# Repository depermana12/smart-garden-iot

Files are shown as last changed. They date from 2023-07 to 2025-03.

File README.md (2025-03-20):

Project ini dibuat sebagai tugas akhir dengan fokus smart garden

## Demo
[Demo alat](https://www.youtube.com/watch?v=bV-0lBpWv4o)

# Tujuan Penelitian
Bertujuan untuk merancang, membuat, mengimplementasi sistem otomasi penyiraman air dan pemupukan cair di dalam mini greenhouse berbasis IoT (Internet of Things).

## Deskripsi singkat

Jadwal penyemprotan pupuk cair menggunakan sensor RTC DS3231, kendali aktuator berdasarkan kelembapan tanah yang menggunakan sensor capacitive soil moisture v1.2, pemrosesan data sensor dilakukan mikrokontroler ESP32. Paket data dikirim menggunakan protocol MQTT ke node-Red Dashboard berbasis web.

Pemantauan dan kendali set point dilakukan pada web. node-RED di-hosting di server dengan nginx sebagai reverse proxy ke domain iot.depermana.com.

## Metode Penelitian
Menggunakan metode rekayasa teknik dengan pengambilan data secara observasi laboratorium. Dimulai dari perancangan, pembuatan, dan pengujian. 

Penerapan penyiraman air menggunakan pendekatan metode metode Blaney-Criddle sebagai perhitungan teoritis kebutuhan air tanaman dengan data iklim BMKG di daerah penelitian. Data tersebut dijadikan acuan kebutuhan penyiraman air

## Perancangan
### blok diagram


### skematik
Imgur

### pcb shield
Imgur

### miniatur green house
Imgur

# Fitur Utama
- Penyiraman otomatis berdasarkan data kelembaban tanah.
- Pemupukan otomatis dengan jadwal yang dapat disesuaikan.
- water level tangki air dan pupuk cair
- suhu dan kelembapan udara GH
- Monitoring kondisi tanaman secara real-time.
- Kendali jarak jauh melalui web.
- data logger menggunakan time series database influx-db

## Teknologi yang Digunakan
- Mikrokontroller ESP32.
- Protokol MQTT broker mosquitto.
- Sensor kelembaban tanah capacitive soil moisture v1.2.
- RTC DS3231
- Sensor ultrasonik HC-SR04
- Sensor suhu dan kelembapan udara DHT 33
- Platform IoT (server running ubuntu, nginx webserver, node-Red, tld, lets encrypt).

# Tantangan Utama
- satu sensor kelembapan tanah tidak dapat merepresentasi keseluruhan nilai kelembapan tanah. Solusi menggunakan lebih dari 1 sensor kelembapan tanah dibeberapa titik tanah dan nilai terseut dirata-rata
- Keamanan sistem IoT untuk melindungi data dan perangkat.

# Hasil Penelitian
Proyek ini berhasil menghasilkan sistem yang dapat memberikan penyiraman dan pemupukan otomatis untuk tanaman berdasarkan kondisi kelembapan tanah dan jadwal pemupukan cair yang dapat ditentukan pengguna. Sistem ini juga memberikan akses jauh melalui internet untuk pengawasan dan kendali.

Imgur

Imgur 

Imgur

Imgur

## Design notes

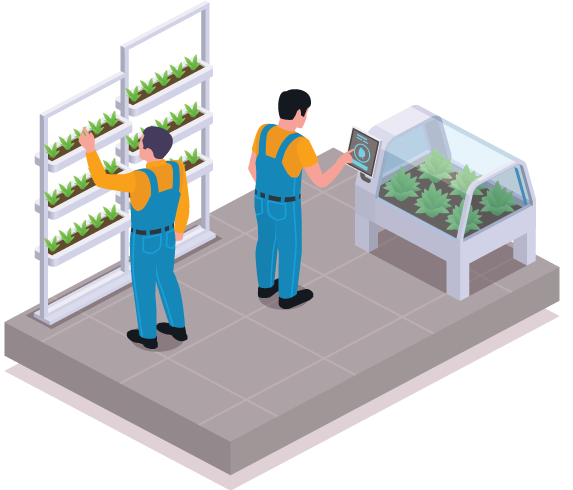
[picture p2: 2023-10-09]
frontend/landing_page/assets/images/right-image.png

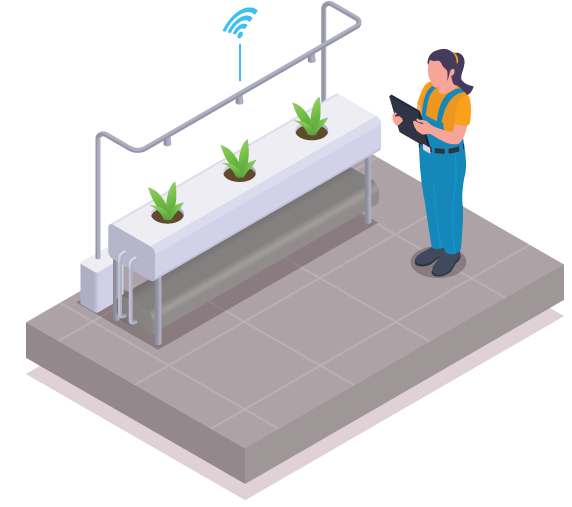
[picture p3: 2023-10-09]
frontend/landing_page/assets/images/left-image.png

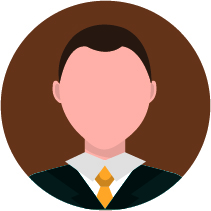
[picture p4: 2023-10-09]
frontend/landing_page/assets/images/member-02.jpg

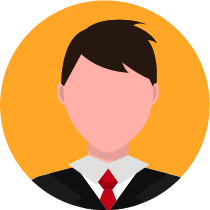
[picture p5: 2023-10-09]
frontend/landing_page/assets/images/member-01.jpg

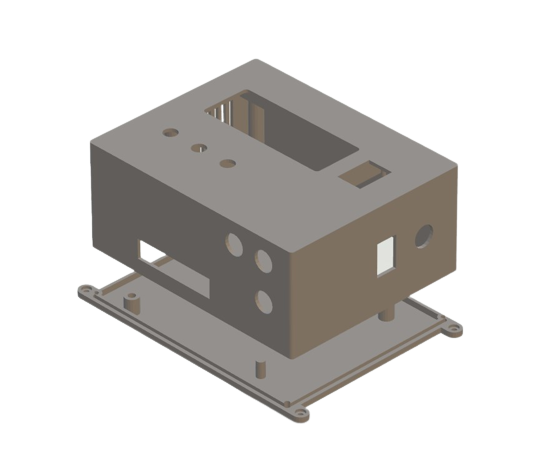
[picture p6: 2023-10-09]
case/casing device.png

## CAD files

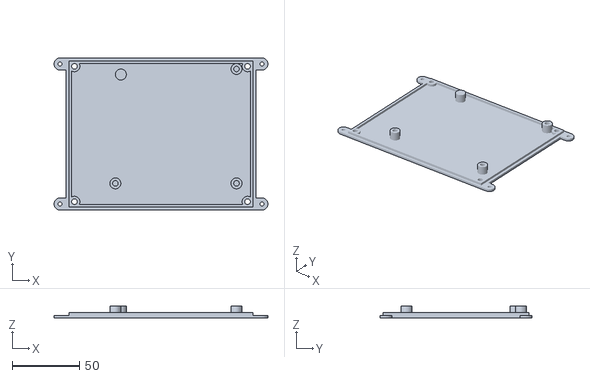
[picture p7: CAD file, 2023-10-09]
case/casing-device-3dp/casing-B.stl
159.0 x 113.0 x 9.00

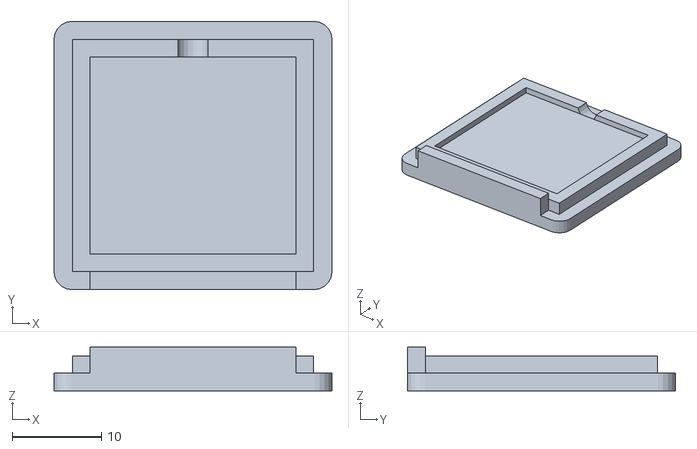
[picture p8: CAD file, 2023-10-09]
case/soil-moisture-3dp/SM-T.stl
31.1 x 30.0 x 4.90

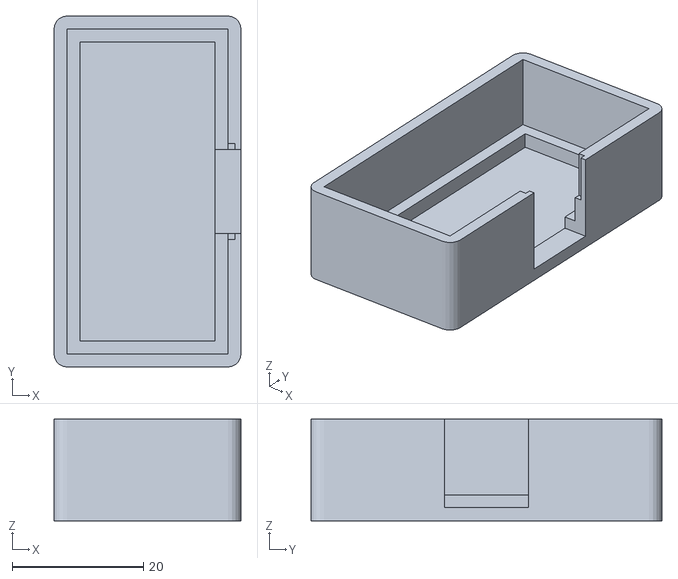
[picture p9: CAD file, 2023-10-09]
case/ultrasonic-case-3dp/USB.stl
28.5 x 53.5 x 15.5

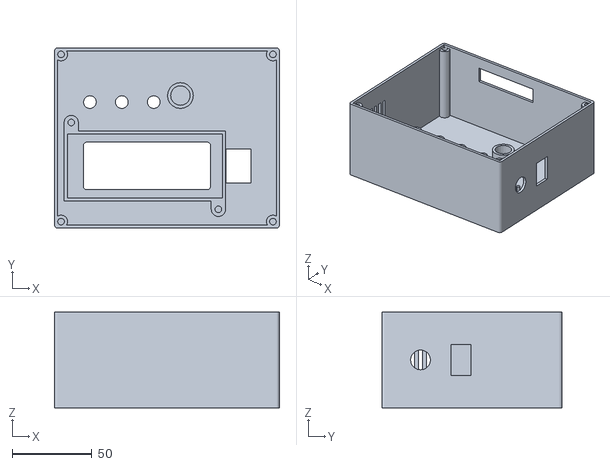
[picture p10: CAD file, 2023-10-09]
case/casing-device-3dp/casing-T.stl
141.0 x 113.0 x 60.0

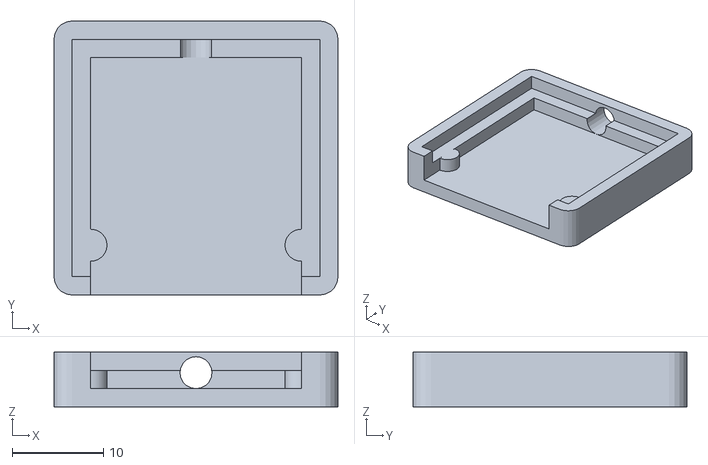
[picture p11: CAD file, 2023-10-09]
case/soil-moisture-3dp/SM-B.stl
31.1 x 30.0 x 6.00

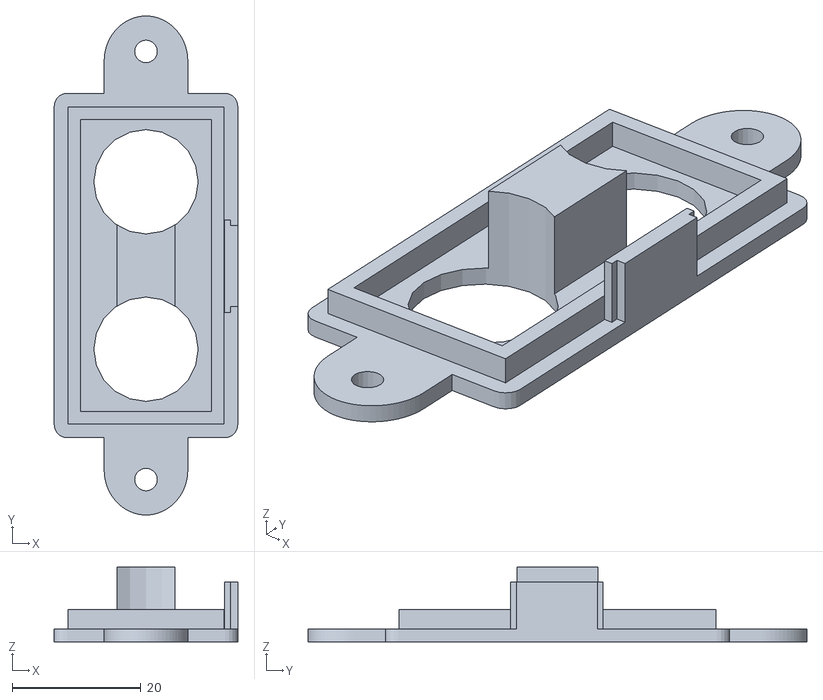
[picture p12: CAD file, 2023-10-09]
case/ultrasonic-case-3dp/UST.stl
28.5 x 77.5 x 11.6

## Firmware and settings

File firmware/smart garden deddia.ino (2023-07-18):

// Deddia Permana
// Changelog History
//
// 19.11.2022
// replaced broken ic ds3231SN RTC
// adjusting calibrating ds3231SN using syncroTime software
// removed poor charging circuit R 201 in RTC board
// 20.11.2022
// fixed relay D2 and D4 active low, setup to high after initialization
// 21.11.2022
// tweaking soil moisture v1.2 into 480khz
// replaced ne555 ic into tlc555 original TI
// 22.11.2022
// created custom charachter icon lcd
// DHT22 set to 2000 millis because hardware low sampling
// 23.11.2022
// Replacing Liquid crystal I2C library with hd44780 library
// added timing for lcd backlight on and off
// added depth and distance calculation of water tank and fertilizer tank
// constrain 1-100 percentage soil humidity
// 24.11.2022
// added multiple screen page in lcd
// 25.11.2022
// integrating nodered
// 8.12.2022
// switching to preferences library, EEPROM deprecated
// 13.12.2022
// added nodes persist to save latest set value
// touch up css dashboard
// 14.12.2022 - 27.12.2022
// refactor


/*
*
* dear future me
* when you write this code you were so motivated, add this and that, tinkering this and that.
* i know when we met again, you will be like wtf is this function, how is it work, where is the config directory and such.
* you have an ego to simplify a function and refuse to elaborate with a comments.
*
*
* Here i'am lol, fck
* glad that right now i have openai to explain my own code wkwkwk
*
*/

#include <SPI.h>
#include <Preferences.h>
#include <NewPing.h>
#include "DHT.h"
#include <Wire.h>
#include <hd44780.h>
#include <hd44780ioClass/hd44780_I2Cexp.h>
#include "RTClib.h"
#include <WiFi.h>
#include <AsyncTCP.h>
#include <ESPAsyncWebServer.h>
extern "C" {
#include "freertos/FreeRTOS.h"
#include "freertos/timers.h"
}
#include <AsyncMqttClient.h>

#define SONAR_NUM 2
#define DHTPIN 33
#define DHTTYPE DHT22
#define MQTT_HOST IPAddress(159, 223, 57, 199)
#define MQTT_USERNAME "depermana"
#define MQTT_PASSWORD "gundam123"
#define MQTT_PORT 1883

// Publish Topics
#define MQTT_PUB_TEMP "garden/dht22/temperature"
#define MQTT_PUB_HUM "garden/dht22/humidity"
#define MQTT_PUB_SOIL "garden/soil/soilHum"
#define MQTT_PUB_WATERK "garden/hcsr04/waterK"
#define MQTT_PUB_WATERJ "garden/hcsr04/waterJ"
#define MQTT_PUB_FERTK "garden/hcsr04/fertilizerK"
#define MQTT_PUB_FERTJ "garden/hcsr04/fertilizerJ"
#define MQTT_PUB_LOGW "garden/log/watering"

// Subscribe Topics
#define MQTT_SUB_REL1 "garden/relay/ch1"  // water
#define MQTT_SUB_REL3 "garden/relay/ch3"  // fertilizer
#define MQTT_SUB_TRES "garden/soil/setPoint"
#define MQTT_SUB_MONTH1 "garden/time/fertM1"
#define MQTT_SUB_MONTH2 "garden/time/fertM2"
#define MQTT_SUB_MONTH3 "garden/time/fertM3"
#define MQTT_SUB_DAY1 "garden/time/fertD1"
#define MQTT_SUB_DAY2 "garden/time/fertD2"
#define MQTT_SUB_DAY3 "garden/time/fertD3"
#define MQTT_SUB_HTIME "garden/time/fertH"
#define MQTT_SUB_MTIME "garden/time/fertMin"
#define MQTT_SUB_DURA "garden/time/duration"
#define MQTT_SUB_WTRT "garden/time/watering"

// BOILER PLATE WIFI MANAGER START //

#define _ESPASYNC_WIFIMGR_LOGLEVEL_ 3
#define DISPLAY_STORED_CREDENTIALS_IN_CP false
#include <esp_wifi.h>
#include <WiFiClient.h>
#include <WiFiMulti.h>
WiFiMulti wifiMulti;
#define USE_LITTLEFS true
#define USE_SPIFFS false

#if USE_LITTLEFS
#include "FS.h"
#include <LittleFS.h>

FS *filesystem = &LittleFS;
#define FileFS LittleFS
#define FS_Name "LittleFS"

#endif

//////

#define ESP_getChipId() (ESP.getChipId())
#define FORMAT_FILESYSTEM false
#define MIN_AP_PASSWORD_SIZE 8
#define SSID_MAX_LEN 32
#define PASS_MAX_LEN 64

typedef struct
{
  char wifi_ssid[SSID_MAX_LEN];
  char wifi_pw[PASS_MAX_LEN];
} WiFi_Credentials;

typedef struct
{
  String wifi_ssid;
  String wifi_pw;
} WiFi_Credentials_String;

#define NUM_WIFI_CREDENTIALS 5


typedef struct
{
  WiFi_Credentials WiFi_Creds[NUM_WIFI_CREDENTIALS];
  uint16_t checksum;
} WM_Config;

WM_Config WM_config;

#define CONFIG_FILENAME F("/wifi_cred.dat")
//////

bool initialConfig = false;
#define USE_AVAILABLE_PAGES false
#define USE_STATIC_IP_CONFIG_IN_CP false
#define USE_ESP_WIFIMANAGER_NTP false
#define USE_CLOUDFLARE_NTP false
#define USING_CORS_FEATURE false

////////////////////////////////////////////

// Use USE_DHCP_IP == true for dynamic DHCP IP, false to use static IP which you have to change accordingly to your network
#if (defined(USE_STATIC_IP_CONFIG_IN_CP) && !USE_STATIC_IP_CONFIG_IN_CP)
// Force DHCP to be true
#if defined(USE_DHCP_IP)
#undef USE_DHCP_IP
#endif
#define USE_DHCP_IP true
#else
// You can select DHCP or Static IP here
#define USE_DHCP_IP true
//#define USE_DHCP_IP     false
#endif

#if (USE_DHCP_IP)
// Use DHCP
#if (_ESPASYNC_WIFIMGR_LOGLEVEL_ > 3)
#warning Using DHCP IP
#endif

IPAddress stationIP = IPAddress(0, 0, 0, 0);
IPAddress gatewayIP = IPAddress(192, 168, 2, 1);
IPAddress netMask = IPAddress(255, 255, 255, 0);

#endif

////////////////////////////////////////////

#define USE_CONFIGURABLE_DNS false

IPAddress dns1IP = gatewayIP;
IPAddress dns2IP = IPAddress(8, 8, 8, 8);

#define USE_CUSTOM_AP_IP false

IPAddress APStaticIP = IPAddress(192, 168, 100, 1);
IPAddress APStaticGW = IPAddress(192, 168, 100, 1);
IPAddress APStaticSN = IPAddress(255, 255, 255, 0);

#include <ESPAsync_WiFiManager.h>

// SSID and PW for Config Portal
String ssid = "smart garden";
String password = "smartgarden123";

// SSID and PW for your Router
String Router_SSID;
String Router_Pass;

WiFi_AP_IPConfig WM_AP_IPconfig;
WiFi_STA_IPConfig WM_STA_IPconfig;

// BOILER PLATE WIFI MANAGER END //

unsigned long previousMillisBL = 0;
unsigned long intervalBL = 60000;
unsigned long previousMillis1 = 0;
unsigned long previousMillis2 = 0;
unsigned long interval1 = 10000;
unsigned long interval2 = 10000;
unsigned long intervalPolling = 1000;
unsigned long previousMillisFert = 0;
unsigned long previousMillisWtr = 0;
unsigned long previousMillisCheckFert = 0;
unsigned long previousPing0 = 0;
unsigned long previousPing1 = 0;

const int LCD_COLS = 20;
const int LCD_ROWS = 4;
const int waterPump = 16;
const int fertilizerPump = 2;
const int PingPin1 = 13;
const int EchoPin1 = 27;
const int PingPin2 = 25;
const int EchoPin2 = 26;
const int MAX_DISTANCE = 23;
const int waterTankDepth = 22;
const int waterTankLength = 19;
const int waterTankWidth = 19;
const int fertilizerTankDepth = 22;
const int fertilizerTankLength = 19;
const int ferilizerTankWidth = 19;
const int buttonLeft = 18;
const int buttonRight = 19;
const int soilMoisture = 32;
const int AirValue = 3506;
const int WaterValue = 1658;

int tanggal, bulan, tahun, jam, menit, detik, suhu, t, h;
int jadwalBulan1, jadwalBulan2, jadwalBulan3, jadwalTanggal1, jadwalTanggal2, jadwalTanggal3, setJam, setMenit;
int soilMoistRaw, soilMoistPercen, soilMoistSetpoint;
int gapSensor = 5;
int percenWaterDepth;
int intervalFertilizer;
int intervalWatering = 5000;
int lcdPageCounter = 1;

float waterMax, waterMin, waterGap;
float waterVolume, fertilizerVolume, waterDistance, fertilizerDistance, waterDepth, fertilizerDepth;

String hari, myDate, myTime, myTemp;

bool currentButtonLeft = LOW;
bool lastButtonLeft = LOW;
bool lastButtonRight = LOW;
bool currentButtonRight = LOW;
bool enableChange = true;
bool backlight = HIGH;
bool overrideCh1 = false;
bool overrideCh3 = false;
bool fertilizerPumpOn = false;
bool wateringOn = false;
bool soilMoistureTriggerActive = false;
bool debounce(bool last, int pin) {
  boolean current = digitalRead(pin);
  if (last != current) {
    delay(10);
    current = digitalRead(pin);
  }
  return current;
}

// Custom LCD Character
byte soilHum[] = { B00100, B01110, B11111, B11111, B10101, B00100, B11111, B11111 };
byte tempHum[] = { B00100, B01010, B01010, B01110, B01110, B11111, B11111, B01110 };
byte dateClock[] = { B00000, B01110, B10101, B10101, B10111, B10001, B01110, B00000 };
byte pupuk[] = { B01100, B01100, B01000, B00000, B10001, B11111, B11111, B11111 };
byte air[] = { B00100, B01110, B01010, B00000, B10001, B11111, B11111, B11111 };
byte kelembapan[] = { B00000, B00100, B01110, B11111, B11111, B11111, B01110, B00000 };

char daysOfTheWeek[7][12] = { "Minggu", "Senin", "Selasa", "Rabu", "Kamis", "Jumat", "Sabtu" };

NewPing sonar[SONAR_NUM] = {
  // Sensor object array.
  NewPing(PingPin1, EchoPin1, MAX_DISTANCE),
  NewPing(PingPin2, EchoPin2, MAX_DISTANCE)
};

// Instance
Preferences preferences;
DHT dht(DHTPIN, DHTTYPE);
hd44780_I2Cexp lcd;
RTC_DS3231 rtc;
AsyncMqttClient mqttClient;
TimerHandle_t mqttReconnectTimer;
TimerHandle_t wifiReconnectTimer;

void setup() {
  checkSensors();
  preferences.begin("smTres", false);
  Serial.begin(115200);
  dht.begin();
  pinMode(waterPump, OUTPUT);
  pinMode(fertilizerPump, OUTPUT);
  digitalWrite(waterPump, HIGH); // turn off relay when init
  digitalWrite(fertilizerPump, HIGH);
  // LCD custom character
  lcd.createChar(0, soilHum);
  lcd.createChar(1, tempHum);
  lcd.createChar(2, dateClock);
  lcd.createChar(3, pupuk);
  lcd.createChar(4, air);
  lcd.createChar(5, kelembapan);
  lcd.home();

  // MQTT calback function
  mqttReconnectTimer = xTimerCreate("mqttTimer", pdMS_TO_TICKS(2000), pdFALSE, (void *)0, reinterpret_cast<TimerCallbackFunction_t>(connectToMqtt));
  wifiReconnectTimer = xTimerCreate("wifiTimer", pdMS_TO_TICKS(2000), pdFALSE, (void *)0, reinterpret_cast<TimerCallbackFunction_t>(connectToWifi));
  WiFi.onEvent(WiFiEvent);
  mqttClient.onConnect(onMqttConnect);
  mqttClient.onDisconnect(onMqttDisconnect);
  mqttClient.onSubscribe(onMqttSubscribe);
  mqttClient.onMessage(onMqttMessage);
  mqttClient.onPublish(onMqttPublish);
  mqttClient.setServer(MQTT_HOST, MQTT_PORT);
  mqttClient.setCredentials(MQTT_USERNAME, MQTT_PASSWORD);
  connectToWifi();
  setupWifiManager();
}

void loop() {
  multiPageLCD();
  loopWifiManager();

  // Publish sensor data every 10 second
  unsigned long currentMillis1 = millis();
  if (currentMillis1 - previousMillis1 >= interval1) {
    checkTempRh();
    checkSoilMoisture();
    checkTank();

    // Publish an MQTT message on topic garden/dht22/temperature
    uint16_t packetIdPub1 = mqttClient.publish(MQTT_PUB_TEMP, 1, true, String(t).c_str());
    Serial.printf("Publishing on topic %s at QoS 1, packetId: %i", MQTT_PUB_TEMP, packetIdPub1);
    Serial.printf("Message: %.2f \n", t);
    // Publish an MQTT message on topic garden/dht22/humidity
    uint16_t packetIdPub2 = mqttClient.publish(MQTT_PUB_HUM, 1, true, String(h).c_str());
    Serial.printf("Publishing on topic %s at QoS 1, packetId %i: ", MQTT_PUB_HUM, packetIdPub2);
    Serial.printf("Message: %.2f \n", h);
    // Publish an MQTT message on topic garden/soil/temperature
    uint16_t packetIdPub3 = mqttClient.publish(MQTT_PUB_SOIL, 0, true, String(soilMoistPercen).c_str());
    Serial.printf("Publishing on topic %s at QoS 1, packetId: %i", MQTT_PUB_SOIL, packetIdPub3);
    Serial.printf("Message: %.2f \n", soilMoistPercen);

    previousMillis1 = currentMillis1;
  }

  // Publish sensor every 10 second
  unsigned long currentMillis2 = millis();
  if (currentMillis2 - previousMillis2 >= interval2) {
    // Publish an MQTT message on topic garden/hcsr04/water
    uint16_t packetIdPub4 = mqttClient.publish(MQTT_PUB_WATERK, 1, true, String(waterDepth).c_str());
    Serial.printf("Publishing on topic %s at QoS 1, packetId: %i", MQTT_PUB_WATERK, packetIdPub4);
    Serial.printf("Message: %.2f \n", waterDepth);
    // Publish an MQTT message on topic garden/hcsr04/water
    uint16_t packetIdPub5 = mqttClient.publish(MQTT_PUB_WATERJ, 1, true, String(waterDistance).c_str());
    Serial.printf("Publishing on topic %s at QoS 1, packetId: %i", MQTT_PUB_WATERJ, packetIdPub5);
    Serial.printf("Message: %.2f \n", waterDistance);
    // Publish an MQTT message on topic garden/hcsr04/fertilizer
    uint16_t packetIdPub6 = mqttClient.publish(MQTT_PUB_FERTK, 1, true, String(fertilizerDepth).c_str());
    Serial.printf("Publishing on topic %s at QoS 1, packetId: %i", MQTT_PUB_FERTK, packetIdPub6);
    Serial.printf("Message: %.2f \n", fertilizerDepth);
    // Publish an MQTT message on topic garden/hcsr04/fertilizer
    uint16_t packetIdPub7 = mqttClient.publish(MQTT_PUB_FERTJ, 1, true, String(fertilizerDistance).c_str());
    Serial.printf("Publishing on topic %s at QoS 1, packetId: %i", MQTT_PUB_FERTJ, packetIdPub7);
    Serial.printf("Message: %.2f \n", fertilizerDistance);

    previousMillis2 = currentMillis2;
  }

  // Polling schedule every sec
  if (millis() - previousMillisCheckFert >= intervalPolling) {

    checkTime();

    // First schedule
    if (bulan == jadwalBulan1 && tanggal == jadwalTanggal1 && jam == setJam && menit == setMenit && detik == 0 && fertilizerPumpOn == false) {
      fertilizerPumpOn = true;
      previousMillisFert = millis();
      digitalWrite(fertilizerPump, LOW);  // pompa on
    }

    // Second schedule
    else if (bulan == jadwalBulan2 && tanggal == jadwalTanggal2 && jam == setJam && menit == setMenit && detik == 0 && fertilizerPumpOn == false) {
      fertilizerPumpOn = true;
      previousMillisFert = millis();
      digitalWrite(fertilizerPump, LOW);  // pompa on
    }

    // Third schedule
    else if (bulan == jadwalBulan3 && tanggal == jadwalTanggal3 && jam == setJam && menit == setMenit && detik == 0 && fertilizerPumpOn == false) {
      fertilizerPumpOn = true;
      previousMillisFert = millis();
      digitalWrite(fertilizerPump, LOW);  // pompa on
    }

    // Turn off the relay after set of seconds
    if (fertilizerPumpOn == true && (millis() - previousMillisFert) >= intervalFertilizer) {
      fertilizerPumpOn = false;
      digitalWrite(fertilizerPump, HIGH);
    }
  }

  // Soil moisture trigger water pump
if (soilMoistPercen < soilMoistSetpoint)
{
  if (!wateringOn)
  {
    previousMillisWtr = millis(); // Record the start time of watering only if it was not already active
  }
  wateringOn = true;
  soilMoistureTriggerActive = true;
  }
  else
{
  wateringOn = false;
  soilMoistureTriggerActive = false;
}

if (wateringOn && soilMoistureTriggerActive && (millis() - previousMillisWtr >= intervalWatering))
{
  wateringOn = false;
  
  }

/*
 * OVERRIDE RELAY CONTROL
 * override only for turning on and off when relay's state is off
 * not inteded yet to do the opposite
 */

// Override water pump
if (wateringOn || overrideCh1)
{
  digitalWrite(waterPump, LOW);
  }
  else
  {
  digitalWrite(waterPump, HIGH);
  }

  // Preferences value. if key failed to retrieve value, then return 0
  soilMoistSetpoint = preferences.getInt("triggerLv", 0);
  setJam = preferences.getInt("saveJam", 0);
  setMenit = preferences.getInt("saveMenit", 0);
  intervalFertilizer = preferences.getInt("saveDura", 0);
  intervalWatering = preferences.getInt("waterDura", 16);
  jadwalBulan1 = preferences.getInt("saveMonth1", 0);
  jadwalBulan2 = preferences.getInt("saveMonth2", 0);
  jadwalBulan3 = preferences.getInt("saveMonth3", 0);
  jadwalTanggal1 = preferences.getInt("saveDay1", 0);
  jadwalTanggal2 = preferences.getInt("saveDay2", 0);
  jadwalTanggal3 = preferences.getInt("saveDay3", 0);

}

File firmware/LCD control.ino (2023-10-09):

void multiPageLCD() {
  currentButtonLeft = debounce(lastButtonLeft, buttonLeft);
  currentButtonRight = debounce(lastButtonRight, buttonRight);

  // button prev page
  if (lastButtonLeft == LOW && currentButtonLeft == HIGH && enableChange == true) {
    lcd.clear();
    if (lcdPageCounter < 5) {  // Page counter never higher than 5(total of pages)
      lcdPageCounter++;
    } else {

      lcdPageCounter = 1;
    }
  }
  lastButtonLeft = currentButtonLeft;

  // button next page
  if (lastButtonRight == LOW && currentButtonRight == HIGH && enableChange == true) {
    lcd.clear();
    if (lcdPageCounter > 1) {
      lcdPageCounter--;
    } else {
      lcdPageCounter = 5;
    }
  }
  lastButtonRight = currentButtonRight;

  switch (lcdPageCounter) {
    case 1:
      {
        // baris 1
        lcd.setCursor(0, 0);
        lcd.print(myDate);
        lcd.setCursor(12, 0);
        lcd.print(myTime);
        // baris 2
        lcd.setCursor(0, 1);
        lcd.write(1);  // temp
        lcd.setCursor(2, 1);
        lcd.print(t);
        lcd.print((char)223);  // degree
        lcd.print("C");

        lcd.setCursor(11, 1);
        lcd.write(5);  // temp
        lcd.setCursor(13, 1);
        lcd.print(h);
        lcd.print("%");
        // baris 3
        lcd.setCursor(0, 2);
        lcd.write(3);  // pupuk
        lcd.setCursor(2, 2);
        lcd.print(fertilizerVolume);
        lcd.print("L");
        lcd.setCursor(11, 2);
        lcd.write(4);  // air
        lcd.setCursor(13, 2);
        lcd.print(waterVolume);
        lcd.print("L");
        // baris 4
        lcd.setCursor(0, 3);
        lcd.write(0);  // soil hum
        lcd.setCursor(2, 3);
        lcd.print(soilMoistPercen);
        lcd.print("%");

        lcd.setCursor(13, 3);
        lcd.print(intervalWatering/1000);
        lcd.print("s");
        
      }
      break;

    case 2:
      {
        lcd.setCursor(0, 0);
        lcd.print("TANGKI AIR");
        lcd.setCursor(12, 0);
        lcd.print(percenWaterDepth);
        lcd.print("%");
        lcd.setCursor(1, 1);
        lcd.print("Jarak:");
        lcd.setCursor(12, 1);
        lcd.print(waterDistance);
        lcd.print("cm");

        lcd.setCursor(1, 2);
        lcd.print("Kedalaman:");
        lcd.setCursor(12, 2);
        lcd.print(waterDepth);
        lcd.print("cm");

        lcd.setCursor(1, 3);
        lcd.print("Volume:");
        lcd.setCursor(12, 3);
        lcd.print(waterVolume);
        lcd.print("l");
      }
      break;

    case 3:
      {
        lcd.setCursor(0, 0);
        lcd.print("TANGKI PUPUK CAIR");
        lcd.setCursor(1, 1);
        lcd.print("Jarak:");
        lcd.setCursor(12, 1);
        lcd.print(fertilizerDistance);
        lcd.print("cm");

        lcd.setCursor(1, 2);
        lcd.print("Kedalaman:");
        lcd.setCursor(12, 2);
        lcd.print(fertilizerDepth);
        lcd.print("cm");

        lcd.setCursor(1, 3);
        lcd.print("Volume:");
        lcd.setCursor(12, 3);
        lcd.print(fertilizerVolume);
        lcd.print("l");
      }
      break;


    case 4:
      {
        lcd.setCursor(0, 0);
        lcd.print("JADWAL PUPUK");
        lcd.setCursor(0, 1);
        if (jadwalTanggal1 < 10) lcd.print("0");
        lcd.print(jadwalTanggal1);
        lcd.setCursor(2, 1);
        lcd.print("/");
        lcd.setCursor(3, 1);
        if (jadwalBulan1 < 10) lcd.print("0");
        lcd.print(jadwalBulan1);
        lcd.setCursor(7, 1);
        lcd.print(setJam);
        lcd.setCursor(9, 1);
        lcd.print(":");
        lcd.setCursor(10, 1);
        lcd.print(setMenit);
        lcd.setCursor(13, 1);
        lcd.print("WIB");

        lcd.setCursor(0, 2);
        if (jadwalTanggal2 < 10) lcd.print("0");
        lcd.print(jadwalTanggal2);
        lcd.setCursor(2, 2);
        lcd.print("/");
        lcd.setCursor(3, 2);
        if (jadwalBulan2 < 10) lcd.print("0");
        lcd.print(jadwalBulan2);

        lcd.setCursor(0, 3);
        if (jadwalTanggal3 < 10) lcd.print("0");
        lcd.print(jadwalTanggal3);
        lcd.setCursor(2, 3);
        lcd.print("/");
        lcd.setCursor(3, 3);
        if (jadwalBulan3 < 10) lcd.print("0");
        lcd.print(jadwalBulan3);
      }
      break;

    case 5:
      {
        lcd.setCursor(0, 0);
        lcd.print("Wi-Fi connected to:");
        lcd.setCursor(0, 1);
        lcd.print(WiFi.SSID());
        lcd.setCursor(0, 2);
        lcd.print("IP address: ");
        lcd.setCursor(0, 3);
        lcd.print(WiFi.localIP());
      }
      break;
  }

  // Backlight LCD
  unsigned long currentMillisBL = millis();
  if (currentMillisBL - previousMillisBL > intervalBL) {
    previousMillisBL = currentMillisBL;
    backlight = LOW;
    enableChange = false;
  }

  if (digitalRead(buttonLeft) == HIGH || digitalRead(buttonRight) == HIGH) {
    previousMillisBL = currentMillisBL;
    if (backlight == LOW) {
      backlight = HIGH;
    } else {
      enableChange = true;
    }
  }

  if (backlight == HIGH) {
    lcd.backlight();
    lcd.display();
  }
  if (backlight == LOW) {
    lcd.noBacklight();
    lcd.noDisplay();
  }
}

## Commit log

2023-04-06 latest node-Red flows
2023-06-08 Update node-RED flows.json
2023-06-10 remove lcd pump status debug
2023-07-18 update some function and fixed bug
    [LCD control.ino, MQTT.ino, smart garden deddia.ino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]
2023-10-09 reorganize file structure
    [SM-B.stl, SM-T.stl, USB.stl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]
